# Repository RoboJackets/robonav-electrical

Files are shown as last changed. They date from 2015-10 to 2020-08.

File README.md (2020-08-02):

RoboNav Electrical
==========
Welcome to the electrcial repository of the RoboNav team! 

## Recommended Software (free)
- a [github account](https://github.com/join?source=header-home) 
    - the centralized location for all common files
- [git](https://git-scm.com/downloads)
    - popular version control system
    - quick [tutorial](https://try.github.io/levels/1/challenges/1)
- [EAGLE](https://www.autodesk.com/education/free-software/eagle)
    - CAD software for designing printed circuit boards (PCBs)

## Cloning the Repository
Now that you have all the required software, it's time to clone the repo!

To clone the repo, nagivate to the location in your computer where you would
like the repository using the change directory command in your terminal (cd):

```
cd desired-location
```

Now its time to clone:

```
git clone https://github.com/RoboJackets/robonav-electrical.git
```

You now have all you need to start contributing to the RoboNav Electrical team!

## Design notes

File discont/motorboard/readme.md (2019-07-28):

Motorboard has been renamed to logic board. The new files can be found on the upper level of directory

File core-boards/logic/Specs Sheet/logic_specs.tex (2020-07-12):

\documentclass[letterpaper, 12pt]{article}
\usepackage[letterpaper,margin=1in]{geometry}
\usepackage[english]{babel}
\usepackage{graphicx}
\usepackage{hyperref}
\usepackage{booktabs}
\usepackage[explicit]{titlesec}
\usepackage{fancyhdr}
\usepackage{inputenc}
\usepackage{enumitem,amssymb}
\usepackage{tikz}
\usetikzlibrary{arrows.meta}
\usetikzlibrary{calc}
\pagestyle{fancy}

\titleformat{\section}
  {\normalfont\Large\bfseries}{\thesection}{1em}{\hyperlink{sec-\thesection}{#1}
\addtocontents{toc}{\protect\hypertarget{sec-\thesection}{}}}
\titleformat{name=\section,numberless}
  {\normalfont\Large\bfseries}{}{0pt}{#1}
  
\titleformat{\subsection}
  {\normalfont\large\bfseries}{\thesubsection}{1em}{\hyperlink{subsec-\thesubsection}{#1}
\addtocontents{toc}{\protect\hypertarget{subsec-\thesubsection}{}}}
\titleformat{name=\subsection,numberless}
  {\normalfont\large\bfseries}{\thesubsection}{0pt}{#1}

\titleformat{\subsubsection}
  {\normalfont\large\bfseries}{\thesubsubsection}{1em}{\hyperlink{subsec-\thesubsubsection}{#1}
\addtocontents{toc}{\protect\hypertarget{subsec-\thesubsubsection}{}}}
\titleformat{name=\subsubsection,numberless}
  {\normalfont\large\bfseries}{\thesubsubsection}{0pt}{#1}

\newlist{todolist}{itemize}{2}
\setlist[todolist]{label=$\square$}
\usepackage{pifont}
\newcommand{\cmark}{\ding{51}}%
\newcommand{\xmark}{\ding{55}}%
\newcommand{\done}{\rlap{$\square$}{\raisebox{2pt}{\large\hspace{1pt}\cmark}}%
\hspace{-2.5pt}}
\newcommand{\wontfix}{\rlap{$\square$}{\large\hspace{1pt}\xmark}}

\begin{document}

\begin{titlepage}
\centering
	{\LARGE RoboJackets IGVC}\\
	\vspace{1cm}
	{\Large IGVC Logic Board 2019}\\
	\vfill
	{\large Created at November 18, 2017}\\
	\vspace{1cm}
	{\large Last Edited at \today\par}
\end{titlepage}

\tableofcontents

\pagebreak
% \section*{Todo Lists}
% \begin{todolist}
%   \item[\done] Update system diagram
%   \item[\done] Update relevant info
%   \item Schematics?
%   \item[\done] Sabertooth pinout
%   \item[\done] Indicator meaning
%   \item Lidar lites
%   \item Firmware
%   \item[\done] Estop system
% \end{todolist}

% \pagebreak

\section{Overview}
This document documents the functionality of the Logic Board (previously referred as \emph{motor board},
or Motor and Light Control Board in the year 2017 - 2018) in the IGVC subteam in \emph{RoboJackets}.
This document aims at providing the reader with the board's capability and limitation. \vspace{6pt}\\
The logic board is the interface between IGVC's software team and her actuators. Software team completes
path and motion planning in the onboard computer and sends driving commands via Ethernet to mbed on the Logic
Board, which then converts to Serial message to the Sabetooth motor controller.\\
\input{system_diagram.tex}

The primary function of the logic board contains the following:
\begin{itemize}
    \item Relay motor commands from software stack to motor controller and perform control algorithm in the process.
    \item Monitoring battery voltage and estop status, relay both to software stack.
    \item Communicate with the rest of electrical system and relay necessary information to the software stack.
\end{itemize}
Previous version of Logic board (motor and light) contains legacy interface for Open Source Motor Controller (OSMC)
which has been removed from the current version.

The motor board is controlled by an mbed NXP LPC1768 microcontroller development board (referred as mbed in the following). More details here: \url{https://os.mbed.com/platforms/mbed-LPC1768/} \vspace{6pt}\\
\pagebreak

\section{Hardware}
The motor board is designed using AutoDesk EagleCAD. Currently the PCB design files can be find under branch \texttt{rev/logic}
of \texttt{igvc-electrical} repository. Here's a link to master branch: \url{https://github.com/RoboJackets/igvc-electrical/}.

\subsection{Power System}
Four voltage level runs through this board. 
\begin{table}[h]
  % \boxed{
    \caption{Summary of functions of Voltage Levels}
    \centering
    \begin{tabular}{p{3cm}p{4cm}p{4cm}}
    \toprule
    Level ($V$)  & Direct Input Source & Maximum Ampere \\
    \midrule
    24V  & Robot Battery & ? \\
    12V  & 12V Rail & 3A  \\
    5V  & 12-5 Regulator & 1A \\
    3V3 & 5-3.3 Regulator & 300mA \\
    \bottomrule
    \end{tabular}
  % }
\end{table}

24V does not have a power plane on the motor board. The sole purpose of having 24V running
through this board is for battery voltage monitor. 24V will be divided between a 4.7k and
a 510 $\Omega$ resistor to achieve a voltage level of maximum 2.34V. The mbed reads in this value
from Analog pin \texttt{p19} to monitor the battery voltage. 

\begin{equation}
    V_{batt} = V_{in} \times 3.3 \times (4700 + 510) / 510 
\end{equation}

\vspace{1em}The rest of the power planes are shown on Figure \ref{fig:pwr_plane}.\\

12V plane is the main power source for the motor board. 12V plane powers the 5V plane via
12V-5V regulator (T1). LED under-glow, flood light and safety light resides on this power
plane. Each with components of sufficient ampere rating. \\

5V plane powers the mbed, encoder and the USB port to the PC. 5V plane powers the 3V3 plane
via the 5V-3V3 regulator, while the 3V3 plane only powers the imu and the ethernet port. \\

\begin{figure}[h]
\centering
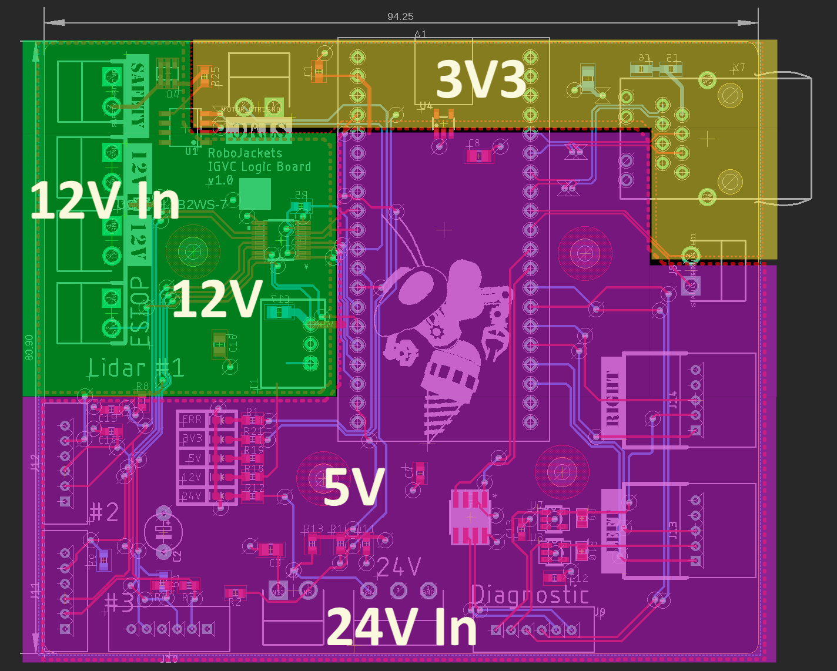
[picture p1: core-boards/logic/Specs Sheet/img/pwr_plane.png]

\caption{Power Plane Indication} \label{fig:pwr_plane}
\end{figure}

Each power plane has a dedicated LED indicator, indicating that this specific power plane
has been powered up. Notice that when \textbf{only} USB(either to mbed or X1 port) is connected,
without 12V power, 12V LED may still light up. This is caused by the internal design of 12-5 regulator.
The fact that 12V LED will light up only dimly suggest that 12V plane does not run 12V at this point.
It is \textbf{STRONGLY DISCOURAGED} to power the logic board solely by the mbed or USB port.

\begin{figure}[h]
  \centering
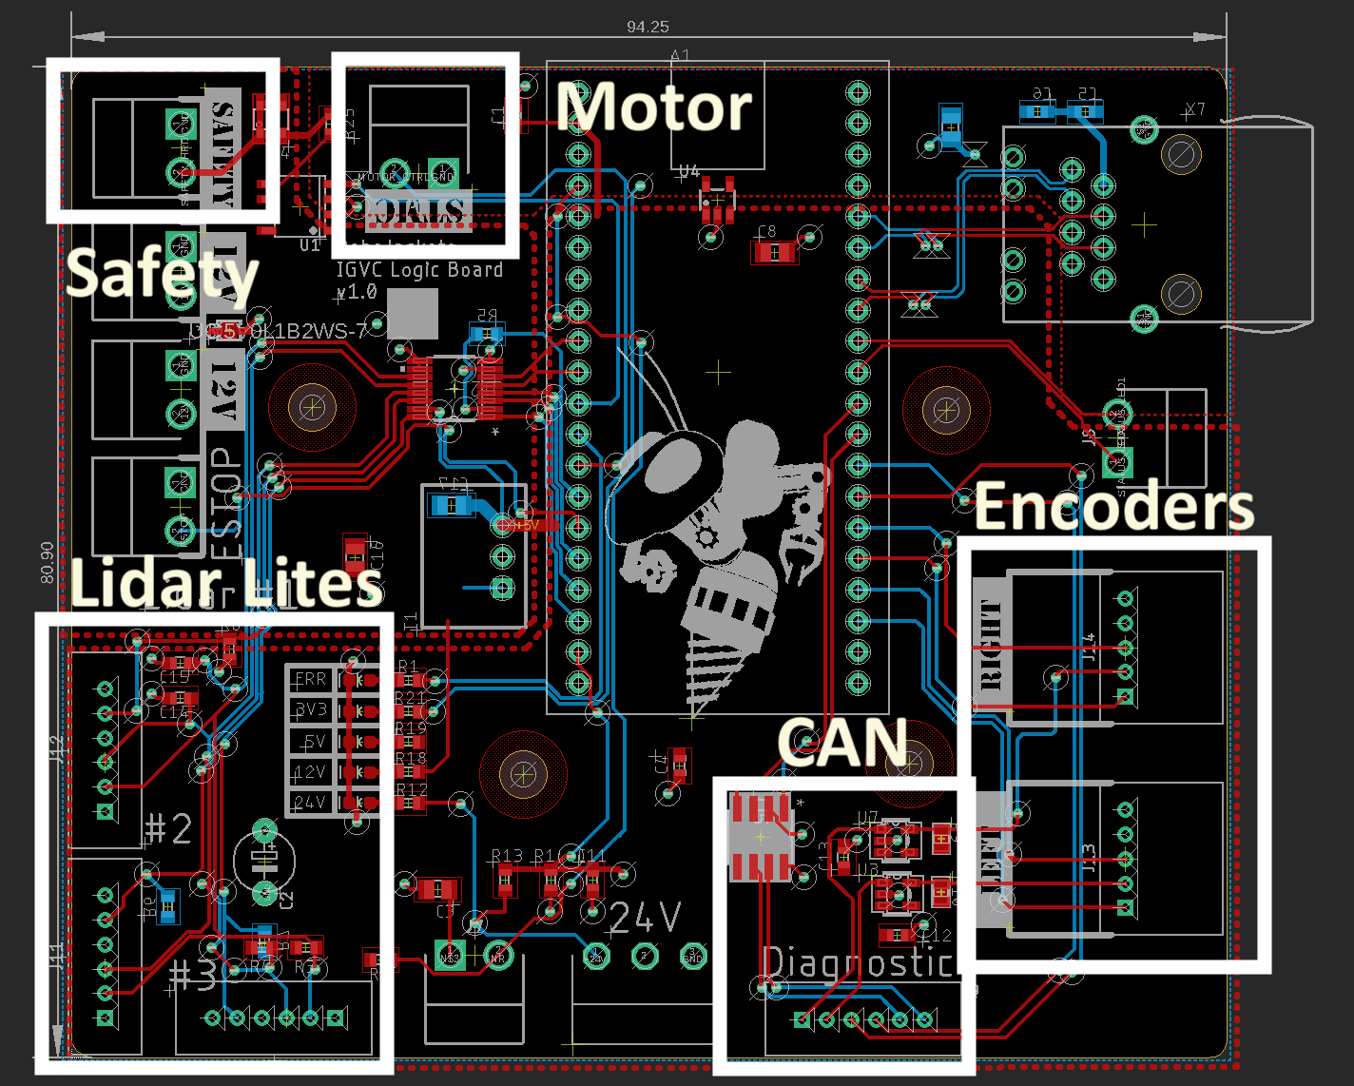
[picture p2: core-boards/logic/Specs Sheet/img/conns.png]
  
  \caption{Power Plane Indication} \label{fig:conns}
  \end{figure}

\subsection{Motor Control}

The connection port on the board can be found labeled in Figure \ref{fig:conns}.

Logic board interface with an off-the-shelf motor controller to control the IGVC motors. Logic board itself
does not run any high power current through the board. Motors on the IGVC robot is controlled by the
Sabertooth 2x60 A motor controller. Data sheets can be found here:
\url{https://www.dimensionengineering.com/products/sabertooth2x60}.\\

Motor board communicate with Sabertooth motor controller via a one-line serial communication
(the "Simplified Serial Communication" Mode). Only \textbf{tx} line on mbed is used, Sabertooth
does not send back any data and \textbf{rx} line on mbed may leave as not connected and used
for other purposes.\\

Port S1 is used for connection to sabertooth motor controller. The serial line connects to port
S1 on the sabertooth motor controller. For switch and other specific configurations, please refer
to the Sabertooth data sheet listed earlier. \\

The Logic board receives motor measurements through optical rotary encoders each with channel A and B.
Every change\footnote{or rise or fall, depending in firmware implementation} in tick would trigger an interrupt
function in the mbed code that increments the counter for angular displacement calculation. 

\subsection{Light Control}
Logic board controls the indicator light.\\

The indicator light is required by the competition rule that it should display different pattern
with regards to whether the robot is powered on or not and in autonomous mode or not. 
Logic board controls whether the light safety light is in flashy mode. The control signal comes from
the software stack.

Previously the motor and light Board contains a functionality for controlling underglows. This has been
moved offboard to a standalone board.

\subsection{Lidar Lites}

The lidar lites are for the concept of virtual bumper. Virtual bumper serves as an extra layer of sanity check to inform
the software stack that the robot is getting dangerously close to an obstacle. \\

The virtual bumper are formed via three Lidar Lites v3 water proof version that points outwards in forward, left and right 45 degrees fashion.
The are linked to the logic board via three six pin connectors and via I$^2$C protocol. Note that three lidar lites shares the same initial 
device address for I$^2$C therefore the design is to sequentially power them up and change the device address so that informations to every device
maybe retrieved. \\

Note that the overwritten device address would be \textbf{reset} after every power cycle. It is necessary to make the sequential power up part of the
regular routine of mbed code startup cycle. 

\subsection{Controller Area Network}

Controller Area Network, or CAN, are adapted on the board so that multiple boards may share the same message bus without the fear that the failure
of any board would bring down the entire network. 

Conventionally, for any micro-controller to join up in a CAN network, it would require that board to talk with a CAN controller, which then in turn
talk to the CAN transceiver that communicate on the CAN bus. The mbed has a built-in CAN controller and only a transceiver is present on the board. 
Be advised that the design of other board would require both a CAN controller and a CAN transceiver. 

\pagebreak

\section{Firmware}
Logic board firmware is currently undergoing an overhaul lead by Dallas Downing. You can find the code in 
\url{https://github.com/RoboJackets/igvc-firmware/tree/master/src/mbed}. mbed communicates with the computer via Ethernet
and Google's Protobuf library. 

\section{Control}
\subsection{PID Algorithm}
For software team to have a reliable localization, control over exact speed of motors are required.\\

Such control is done through PID algorithm in the motor board. PID stands for Proportional-Integral-Derivative controller. It operates on the idea that the output is changed based on the proportional, derivative and integral of difference between desired speed and actual speed over a certain $dT$. Details see \url{https://en.wikipedia.org/wiki/PID_controller}\\

Parameter values P, I and D need to be tuned for every different system. Increase proportional term value will increase the speed of the control system response, but will enlarge the overshoot and cause oscillation. Increase derivative term will cause the control system to react more strongly to changes in the error term, but will make the system unstable if the feedback signal is noisy. Increase integral term will sum overtime and drive the Steady-state error to zero, but will also increase the risk of a phenomenon called integral windup. \\

In short, PID need to be tuned, manually, especially if you're reading this document, since the robot probably has gone through a major remake and the system transfer function for the gear box + robot has changed.

\subsection{Emergency Stop}
In the event of IGVC robot goes terminator, absolute control over motor is required.\\

Emergency stop is the hardware stop for our robot that will physically cut power to motors,
done via a solenoid with diode magic circuits. The significance of Estop to the logic board
is that if the motors are cut power and motor board is still running PID algorithm, PID will
think power increase is not resulting in reduction of error, thus increase power output and
eventually reach maximum. When the robot is re-enabled, such error may cause robot to tip over. \\

A port is added to the motor board to accommodate this issue. Port marked "Estop" is for monitoring
estop status. In current electrical system design, when robot is stoped, this port will receive a +5V
signal and will be left floating when robot is enabled. This floating signal is complemented by mbed
pin's internal pull down configuration. 

This signal is further relayed to software stack in \texttt{robot enabled}. The logic board itself
does not perform any functionality in the estop system and does not need to be onboard the robot to test
the estop system.

\section{Miscellaneous}
\subsection{Expected Future Usage}
When the motor board was first designed, we left a ethernet port that was eventually utilized by IGVC for their
stability over simulated Serial port. So much that we have retired the USB port on the logic board. It is hard to
imagine what can be used for the future version of the logic board, since the control board now requires a major
revision as IGVC move towards swerve drive. There are always things to be done on the software level. It is not
hard to implement sensor fusion on the mbed and people should consider that possibility. After all, it is only
a small  embedded platform, robustness is of the most importance.

\subsection{Special Regards}
The author would like to thank Evan Peterson and Ryo Osawa from RoboJackets RoboCup team for their
awesome help in reviewing the design of board and much helpful advice. He would also like to thank
Jason Gibson from RoboJackets IGVC software team for his time in debugging Serial communication
problems with NUC.  

\subsection{Legacy Interfaces}
\textbf{NOT PRESENT IN LOGIC BOARD!}\\
IGVC robot Woodi (Year 2016 - 2017) and her predecessors used 4 Open Source Motor Controller (Referred as OSMC in the following) to control its motors. Current IGVC robot Jessi no longer uses OSMCs, yet a legacy port is reserved on the motor board in case for any unexpected incident. \vspace{6pt}\\
OSMCs are essentially H-bridge DC motor control circuits. Due to the specific design of OSMC, both switches on the high side of H-bridge are hard-wired to \textbf{CLOSED}. Therefore speed and direction control solely depends on the value of low side switches (see OSMC datasheet for specific control logic). The mbed has direct control over the low-side switches via PWMOut pins from p21 to p24. Be advised that one should \textbf{NEVER} set two low switches on the same H bridge to \textbf{CLOSED} at \textbf{ANY TIME}. \vspace{6pt}\\
The motor board used 2 Optoisolators chips to help control the low-side switches. Optoisolators keeps the motor board circuits electrically separated from the motor power circuits. Such design helps to protect the mbed from the fluctuation caused by motors. Although \emph{technically}, the mbed and the motor will still share the same ground level, having them not directly electrically connected through the motor board gives more time for the rest of the system to damp the fluctuation and protect the mbed. \vspace{6pt}\\
OSMC datasheets can be found here:\\
\url{http://www.robotpower.com/downloads/osmc3-22sch-clean.pdf}\\

\end{document}

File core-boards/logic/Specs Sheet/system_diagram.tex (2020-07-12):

% \begin{figure}[h]
%     \centering
%     \includegraphics[width=0.7\textwidth]{UpandLow.png}
%     \caption{motor board's Data Input and Output}
%     \end{figure}

\begin{figure*}[th]
    \centering
    \begin{tikzpicture}[inner sep=1em]
        \node[anchor=center, draw=black, rounded corners,] (pc) at (0in, 0in) {Computer};
        \node[anchor=center, draw=black, rounded corners,] (logic) at (0in, -1in) {Logic Board};
        \draw[{Latex[length=3mm]}-{Latex[length=3mm]}](pc.south)--(logic.north);
        \node[anchor=west] (ethernet) at (-0.5in, -0.5in) {Ethernet};

        \node[anchor=center, draw=black, rounded corners,] (sabertooth) at (-2in, -1in) {Sabertooth};
        \draw[{Latex[length=3mm]}-{Latex[length=3mm]}] (sabertooth.east)--(logic.west);
        \node[anchor=south] (serial) at (-1in, -1in) {Serial};
        \node[anchor=center, draw=black, rounded corners,] (motor) at (-2in, 0in) {Motor};
        \draw[{Latex[length=3mm]}-{Latex[length=3mm]}] (sabertooth.north)--(motor.south);
        \draw[{Latex[length=3mm]}-{Latex[length=3mm]}] (motor.south east) -- (logic.north west);
        \node[anchor=center, rotate=-27] at (-1in, -0.35in) {Encoder};
 
        \node[anchor=center, draw=black, rounded corners,] (safety) at (2in, 0in) {Safety Light};
        \draw[{Latex[length=3mm]}-] (safety.south west)--(logic.north east);

        \node[anchor=center, draw=black, rounded corners,] (estop) at (2in, -1in) {Estop Status};
        \draw[-{Latex[length=3mm]}] (estop.west)--(logic.east);

        \node[anchor=center, draw=black, rounded corners,] (diag) at (2in, -2in) {Diagnostic Board};
        \draw[{Latex[length=3mm]}-{Latex[length=3mm]}] (logic.south east)--(diag.north west);
        \node[anchor=center, rotate=-40] at (1in, -1.4in) {CAN};

        \node[anchor=center, draw=black, rounded corners,] (vrail) at (0in, -2in) {24V Rail};
        \draw[-{Latex[length=3mm]}] (vrail.north)--(logic.south);

        \node[anchor=center, draw=black, rounded corners,] (lidar) at (-2in, -2in) {Lidar Lites};
        \draw[{Latex[length=3mm]}-{Latex[length=3mm]}] (lidar.north east)--(logic.south west);
        \node[anchor=center, rotate=27] at (-1in, -1.35in) {I$^2$C};

    \end{tikzpicture}
    \caption{Logic board's Data Input and Output}
\end{figure*}

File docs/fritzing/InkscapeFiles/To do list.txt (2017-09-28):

1. Design/Draft info light to overall.fzz
2. Design light shield
3. Design motor shield
4. Design Safety light on

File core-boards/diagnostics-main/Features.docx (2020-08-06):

What do we want the main diagnostic board to do?

1. Main Board Components:
  a. Parts:
    i. ATMEGA2560 (MCU)
    ii. Two Pin Connector
      1. GND / VCC (5v)
    iii. Crystal (16 Mhz) (ECS-160-20-5PX-TR (https://www.digikey.com/product-detail/en/ecs-inc/ECS-160-20-5PX-TR/XC1282TR-ND/765265))
      1. Capacitors x2
    iv. Decoupling Capacitors
    v. Pull Up Resistor
2. Interface with the other mini boards:
  a. Specifically:
    i. Temperature Sensor
    ii. LED Feedback w/ Neopixels
    iii. Current Sensor
    iv. Decoupled Motor Detection
  b. How: Connectors using CAN bus communication or I^2C protocol
  c. What Parts:
    i. 5 Pin Connector (WM18933-ND) x 5
      1. GND / VCC (5v) / SDA / SCL
3. Interface with an external display
  a. How: Radio
  b. What Parts:
4. Interface with the Mast Status Panel:
  a. How: I2C
  b. What Parts:
5. Interface with Logic Board:
  a. How: 5 Pin Connector
  b. What Parts:
6. Interface with the Estop Board:
  a. How: 3 Pin Connector
  b. What Parts:
    i. Two Pin Connector
7. Read/Write to a SD Card
  a. How: SPI directly to the card
  b. What Parts:
    i. SD CARD
    ii. Level Shifter (5v -> 3v3)

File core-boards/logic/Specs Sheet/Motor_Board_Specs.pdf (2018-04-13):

# RoboJackets IGVC

## IGVC Motor and Light Control Board 2017

### Created at November 18, 2017

### Last Edited at April 13, 2018

CONTENTS | CONTENTS

## Contents

1 Overview | 2
2 Hardware | 4
3 Firmware | 7
4 Miscellaneous | 9
5 Special Regards | 10

1

1 OVERVIEW

## 1 Overview

This document explained the function of the Motor and Light Control Board (referred as motor board in the following) on RoboJackets IGVC subteam robot Jessi in the year 2017 - 2018 and showed how the board is designed with regards to its need, capability and limitation. This document is created in the hope that future RJ members can have a good understanding of the robot without unnecessary effort such as staring into the void and cursing whoever did the board without leaving a documentation.

The motor board is the interface between Jessi’s software control and her motor. IGVC software team completes path-planning on the onboard Intel NUC computing unit and will send driving command to the motor board. The motor board will tune the value according to PID and encoder value and then send it to the sabertooth motor controller, which will eventually power the motor.

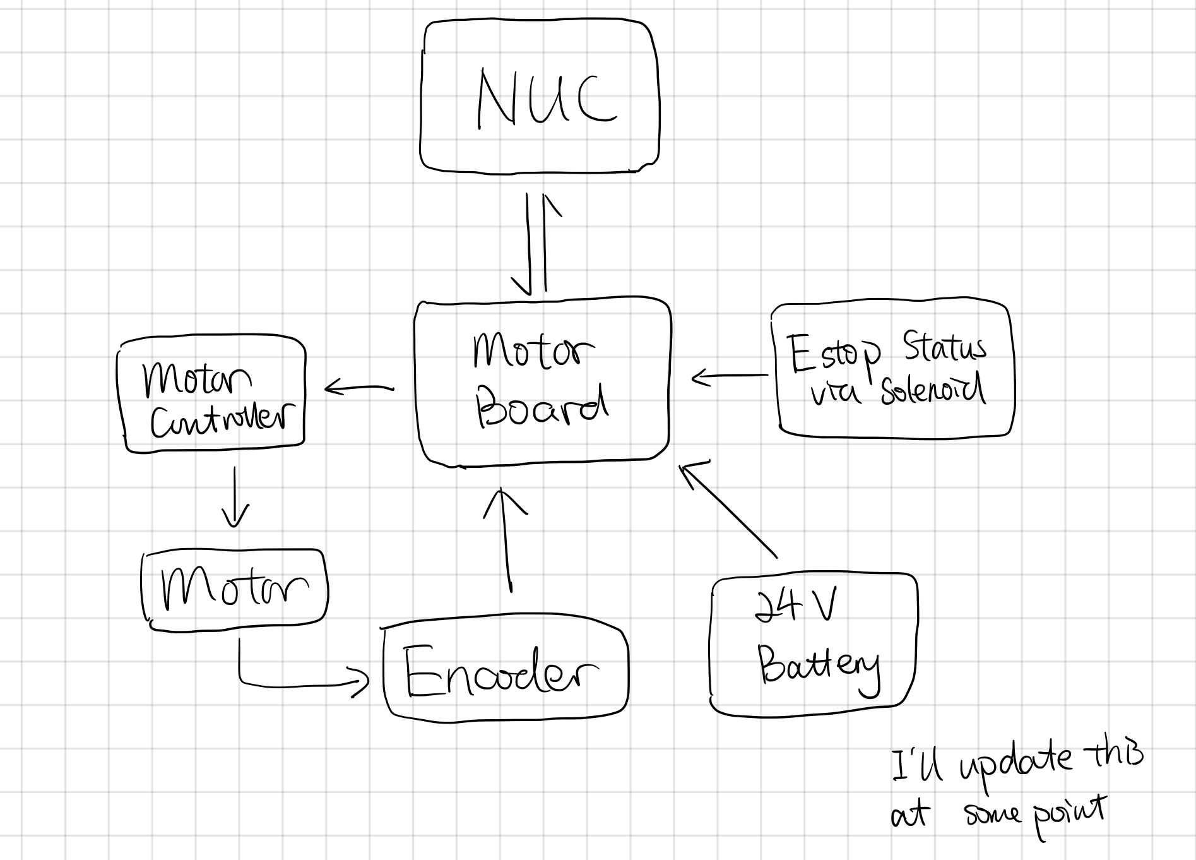
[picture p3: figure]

Figure 1: motor board’s Data Input and Output

The primary function of the motor board is to ensure the DC motors are operating at the speed desired by the NUC. Secondary functions include controlling the LED under-glow, monitoring battery voltage, E-stop status as well as Safety Light. The board also contained two ports for interfacing

2

1 OVERVIEW

with OSMCs, a legacy motor controller module RJ IGVC team used in the past. Each functioning circuits can operate independently from each other.

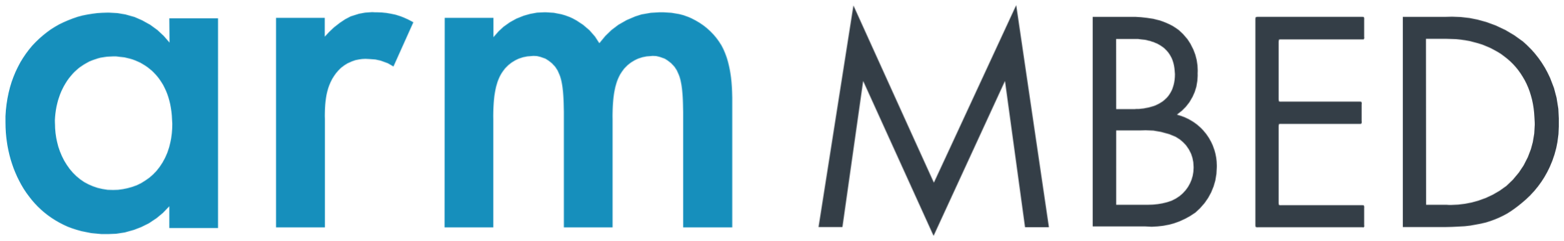
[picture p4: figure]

Figure 2: ARM logo

The motor board is controlled by an mbed NXP LPC1768 microcontroller development board (referred as mbed in the following). More details here: https://os.mbed.com/platforms/mbed-LPC1768/

3

2 HARDWARE

## 2 Hardware

The motor board is designed using AutoDesk EagleCAD. All PCB design files can be found under https://github.com/RoboJackets/igvc-electrical/tree/master/motorboard

### 2.1 Power System

Four voltage level runs through this board.

Table 1: Summary of functions of Voltage Levels
Level (V ) | Direct Input Source | Maximum Ampere
24V | Lithium Battery | ?
12V | 12V Rail | 3A
5V | 12-5 Regulator | 1A
3V3 | 5-3.3 Regulator | 300mA

24V does not have a power plane on the motor board. The sole purpose of having 24V running through this board is for battery voltage monitor. 24V will be divided between a 4.7k and a 510 ohm resistor to achieve a voltage level of maximum 2.34V. The mbed reads in this value from Analog pin p20 to monitor the battery voltage. Vbatt = Vin ∗ 3.3 × (4700 + 510)/510.

12V plane is the main power source for the motor board. 12V plane powers the 5V plane via 12V-5V regulator (T1). LED under-glow, flood light and safety light resides on this power plane. Each with components of sufficient ampere rating.

5V plane powers the mbed, encoder and the USB port to the NUC. 5V plane powers the 3V3 plane via the 5V-3V3 regulator, while the 3V3 plane only powers the imu and the ethernet port.

Each power plane has a dedicated LED indicator, indicating that this specific power plane has been powered up. Notice that when only USB(either to mbed or X1 port) is connected, without 12V power, 12V LED may still light up. This is caused by the internal design of 12-5 regulator. The fact

4

2.2 Motor Control | 2 HARDWARE

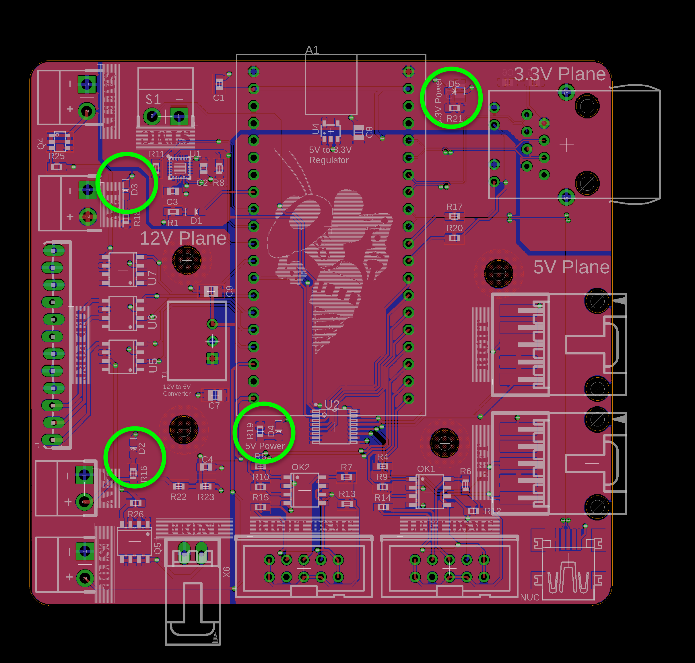
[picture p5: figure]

Figure 3: Power Indictor Circled Out

that 12V LED will light up only dimly suggest that 12V plane does not run 12V at this point. It is discouraged to power the motor board solely by the mbed or USB port.

### 2.2 Motor Control

Motor board interface with a separate motor controller to control the IGVC motors. Motor board itself does not run any high power current through the board. Motors on the IGVC robot is controlled by the Sabertooth 2x60 A motor controller. Data sheets can be found here: https://www.dimensionengineering.com/products/sabertooth2x60.

Motor board communicate with Sabertooth motor controller via a oneline serial communication (the ”Simplified Serial Communication” Mode).

5

2.3 Light Control | 2 HARDWARE

Only tx line on mbed is used, Sabertooth does not send back any data and rx line on mbed may leave as not connected and used for other purposes.

Port S1 is used for connection to sabertooth motor controller. The serial line connects to port S1 on the sabertooth motor controller. For switch and other specific configurations, please refer to the Sabertooth data sheet listed earlier.

### 2.3 Light Control

Motor board controls the indicator light and under-glow light bar.

The indicator light is required by the competition rule that it should display different pattern with regards to whether the robot is powered on or not and in autonomous mode or not. Motor board is capable of controlling such a light via port marked ”SAFETY”. The control signal, however, will come directly from NUC, since it can be implemented easier on NUC.

The under-glow light bar can be controlled directly via motor board. The under-glow is purely an aesthetic feature of the robot. Motor board have control over RGB values via PWMOut pins, (see schematics). The board has been designed to handle the current required.

6

3 FIRMWARE

## 3 Firmware

### 3.1 Interacting with NUC

Motor board communicates with NUC via Serial communication emulated by USBSerial interface. For more details, please see mbed OS 5 API. Serial communication via the onboard USB port

Motor board accepts a number of commands from NUC. At the startup of ROS, NUC would set parameters for PID algorithm and for most of the time, (20Hz and nonstop), NUC will be sending motor commands.The list of commands can be found in the following table, any character in parenthesis is optional. When the source is NUC, it’s always setting the value in motor board. When the source is motor board, it’s always returning a value to the NUC.

Motor board abbreviated as MB

Table 2: Summary of Serial Communication
Preamble | Format | Example | Source | Function
$ | $(-)X.X,(-)X.X | $-1.2,1.3 | NUC | Motor speed
#L | #LX | #L1 | NUC | Indicator light

#P | #PX.X,X.X | #P8.0,8.0 | NUC | PID P value

#D | #DX.X,X.X | #D8.0,8.0 | NUC | PID D value

$ | $(-)X.XX,
| (-)X.XX,0.XXX | $-1.25,1.13
| | ,0.051 | MB | Actual speed & dT
#V | #VXX.XX,X | #V24.23,1 | MB | Battery and Estop

When the communication is directly related to motor, the first value will always be for left motor and second for right. For example $1.2,-1.3 from NUC means the NUC want to set left motor be at 1.2m/s and right motor at reverse −1.3m/s.

7

3.2 Controlling the board | 3 FIRMWARE

### 3.2 Controlling the board

### 3.2.1 PID Algorithm

For software team to have a reliable localization, control over exact speed of motors are required.

Such control is done through PID algorithm in the motor board. PID stands for Proportional-Integral-Derivative controller. It operates on the idea that the output is changed based on the proportional, derivative and integral of difference between desired speed and actual speed over a certain dT. Details see https://en.wikipedia.org/wiki/PID_controller

Parameter values P, I and D need to be tuned for every different system. Increase proportional term value will increase the speed of the control system response, but will enlarge the overshoot and cause oscillation. Increase derivative term will cause the control system to react more strongly to changes in the error term, but will make the system unstable if the feedback signal is noisy. Increase integral term will sum overtime and drive the Steady-state error to zero, but will also increase the risk of a phenomenon called integral windup.

In short, PID need to be tuned, manually, especially if you’re reading this document, since the robot probably has gone through a major remake and the system transfer function for the gear box + robot has changed.

### 3.2.2 Emergency Stop

In the event of IGVC robot goes terminator, absolute control over motor is required.

Emergency stop is the hardware stop for our robot that will physically cut power to motors, done via a solenoid with diode magic circuits. The significance of Estop to the motor board is that if the motors are cut power and motor board is still running PID algorithm, PID will think power increase is not resulting in reduction of error, thus increase power output and eventually reach maximum. When the robot is re-enabled, such error may cause robot to tip over.

8

4 MISCELLANEOUS

A port is added to the motor board to accommodate this issue. Port marked ”Estop” is for monitoring estop status. In current electrical system design, when robot is stoped, this port will receive a +5V signal and will be left floating when robot is enabled. This floating signal is complemented by mbed pin’s internal pull down configuration.

## 4 Miscellaneous

### 4.1 Legacy Interfaces

IGVC robot Woodi (Year 2016 - 2017) and her predecessors used 4 Open Source Motor Controller (Referred as OSMC in the following) to control its motors. Current IGVC robot Jessi no longer uses OSMCs, yet a legacy port is reserved on the motor board in case for any unexpected incident.

OSMCs are essentially H-bridge DC motor control circuits. Due to the specific design of OSMC, both switches on the high side of H-bridge are hardwired to CLOSED. Therefore speed and direction control solely depends on the value of low side switches (see OSMC datasheet for specific control logic). The mbed has direct control over the low-side switches via PWMOut pins from p21 to p24. Be advised that one should NEVER set two low switches on the same H bridge to CLOSED at ANY TIME.

The motor board used 2 Optoisolators chips to help control the low-side switches. Optoisolators keeps the motor board circuits electrically separated from the motor power circuits. Such design helps to protect the mbed from the fluctuation caused by motors. Although technically, the mbed and the motor will still share the same ground level, having them not directly electrically connected through the motor board gives more time for the rest of the system to damp the fluctuation and protect the mbed.

OSMC datasheets can be found here: http://www.robotpower.com/downloads/osmc3-22sch-clean.pdf (http://www.robotpower.com/downloads/osmc3-22sch-clean.pdf)

9

4.2 Expected Future Usage | 5 SPECIAL REGARDS

### 4.2 Expected Future Usage

The motor board contains hardware feature not currently utilized. The Ethernet port (X7) is not currently used and the USB port (X1) is only used as Serial port, implemented as USBSerial in mbed firmware. The routing for traces connecting both port to the mbed have followed the layout rules for differential pair. If higher speed communication between the motor board and on-board computer is desired, these ports may be used.

## 5 Special Regards

The author would like to thank Evan Peterson and Ryo Osawa from Robo-Jackets RoboCup team for their awesome help in reviewing the design of board and much helpful advice. He would also like to thank Jason Gibson from RoboJackets IGVC software team for his time in debugging Serial communication problems with NUC.

10

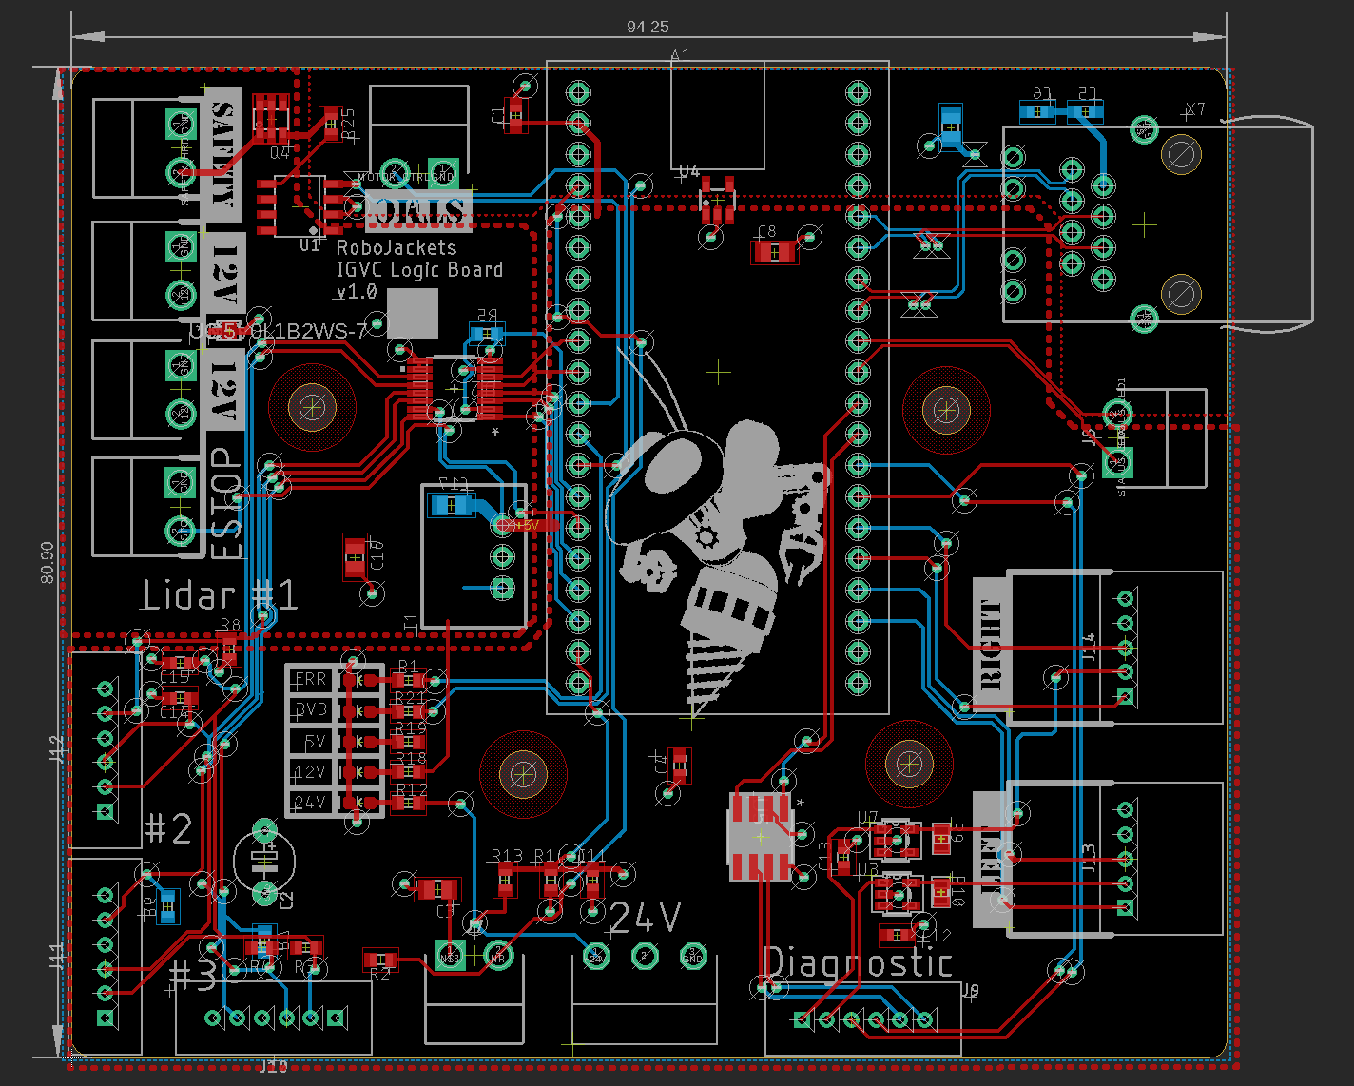
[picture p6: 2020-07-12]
core-boards/logic/Specs Sheet/img/default.png

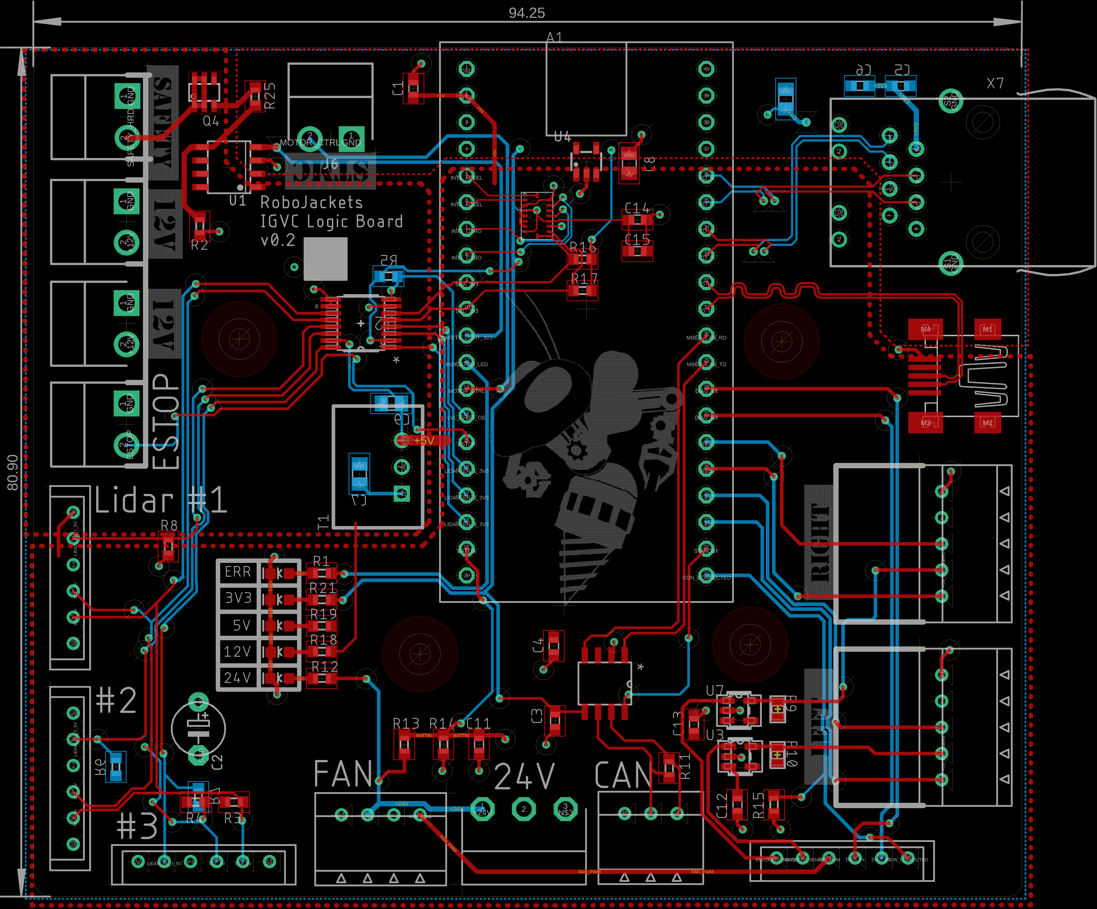
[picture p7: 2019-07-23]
core-boards/logic/Eagle Files/logic.png

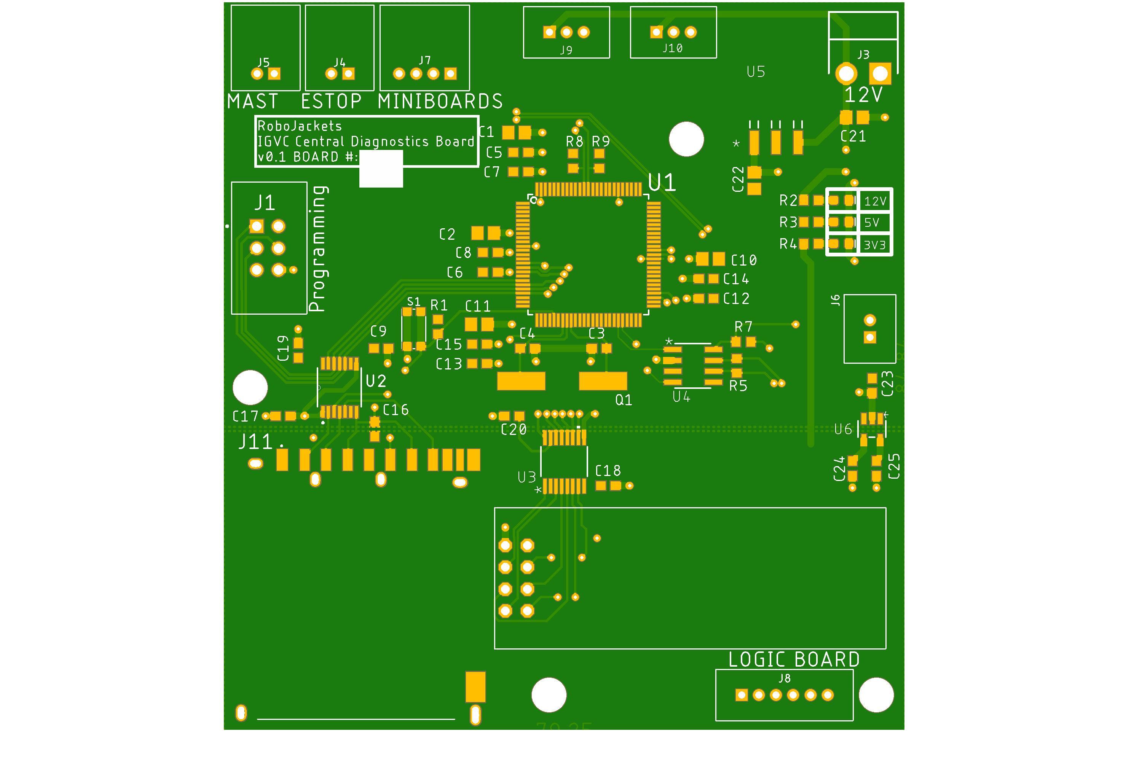
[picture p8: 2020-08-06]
core-boards/diagnostics-main/Eagle Files/diagnostic-main.png

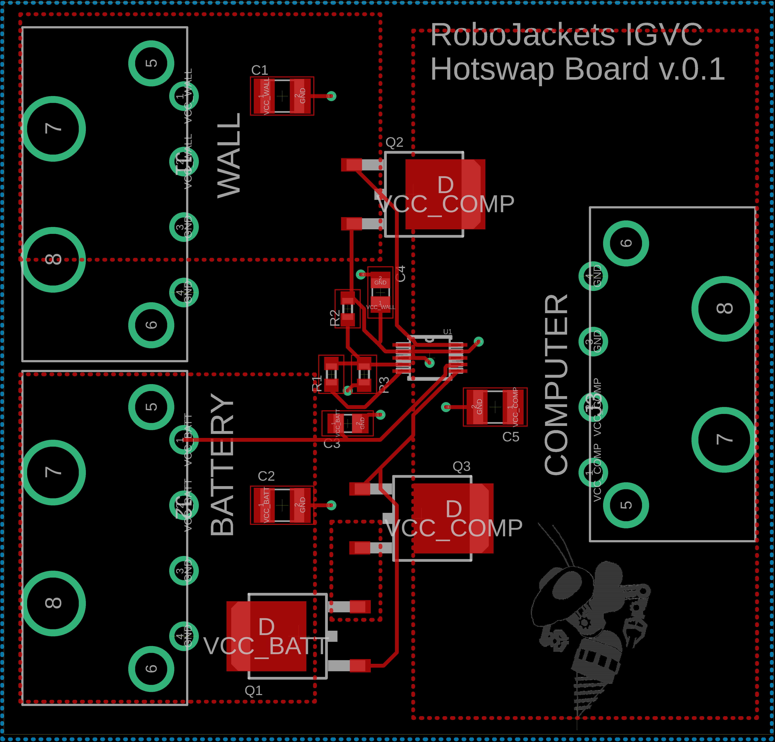
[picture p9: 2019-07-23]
core-boards/hotswap/hotswap.png

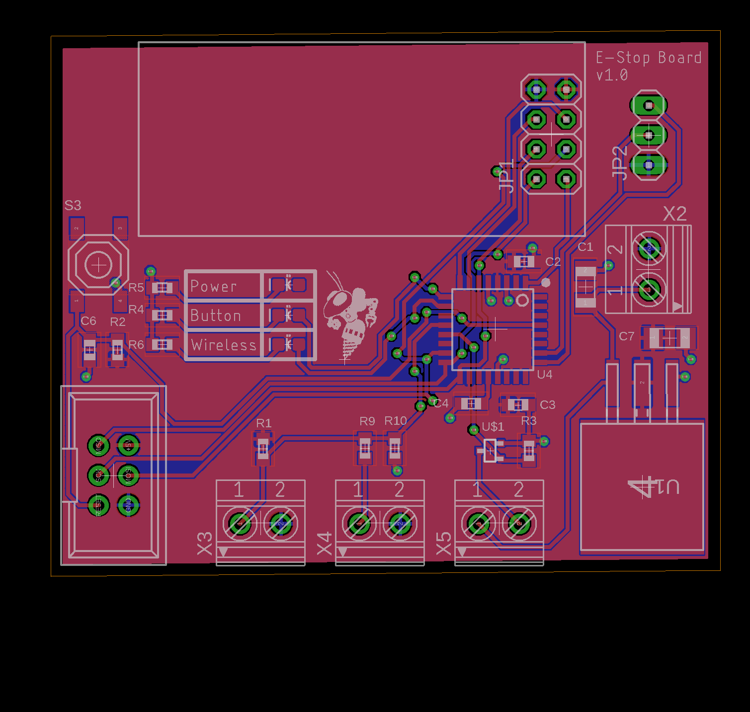
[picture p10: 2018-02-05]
core-boards/estop/Eagle Files/E-Stop Board v1.0.png

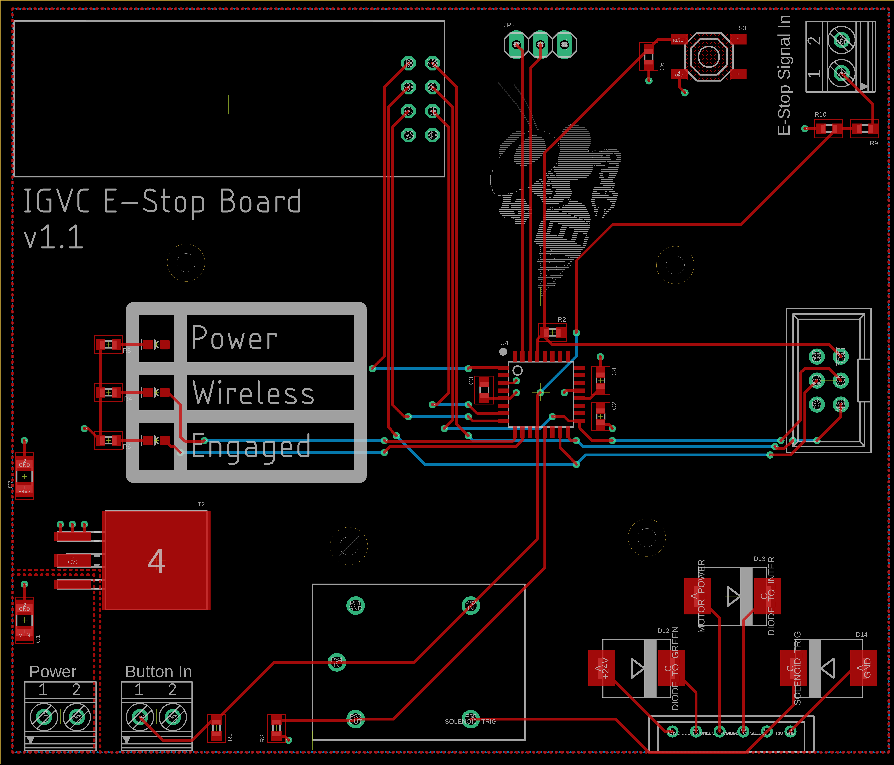
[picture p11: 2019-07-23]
core-boards/estop/Eagle Files/estop.png

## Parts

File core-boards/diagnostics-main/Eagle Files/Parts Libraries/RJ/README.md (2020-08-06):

# RoboJackets Eagle CAD Libraries

This repository contains unified libraries across the RoboJackets teams. New PCB repos should add this as a submodule.

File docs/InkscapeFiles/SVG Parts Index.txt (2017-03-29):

***This file contains all parts from the current IGVC Robot***
12V Lithium-acid Battery
Switch
24V Rail
GPS power Plug
PC battery Controller
E-stop Solenoid
Reciever
Arduino
Shunt
Battery Controller
Current Measure
Motor Shields
Encoder
24V to 12V Converter
Signal Light
E-stop Light
5V Converter

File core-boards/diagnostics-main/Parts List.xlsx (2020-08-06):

Part | Part Number / ID | Package | Digikey Link | #
16 Mhz Crystal | ECS-160-20-5PX-TR |  | https://www.digikey.com/product-detail/en/ecs-inc/ECS-160-20-5PX-TR/XC1282TR-ND/765265 | 1
Capacitor(10uF) | 1276-2405-1-ND | C0805 |  | 6
Capacitor(2.2uF) | 1276-1085-1-ND | C0603 |  | 1
Capacitor(1uF) | 1276-1182-1-ND | C0603 |  | 5
Capacitor(.1uF) | 490-10390-1-ND | C0603 |  | 10
Capacitor(.01uF) | 311-1596-1-ND | C0603 |  | 1
Capacitor(22pF) | 490-17301-1-ND | C0603 |  | 2
Resistor(10k) | 311-10.0KLRCT-ND | R0402 |  | 1
Resistor(2.2k) | 311-2.20KLRCT-ND | R0402 |  | 1
Resistor(1k) | 311-1.00KLRCT-ND | R0402 |  | 2
Resistor(120) | 311-120NCT-ND | R0402 |  | 2
Diode (Green) | P13485CT-ND | LED-0603 | https://www.digikey.com/product-detail/en/panasonic-electronic-components/LNJ326W83RA/P13485CT-ND/970685 | 3
Switch | 401-1426-2-ND | KMR2 | https://www.digikey.com/product-detail/en/c-k/KMR211GLFS/401-1426-2-ND/550475 | 1
Can Bus | 497-3930-1-ND |  | https://www.digikey.com/product-detail/en/microchip-technology/MCP2551T-I-SN/MCP2551T-I-SNCT-ND/9698145 | 1
Can Controller | MCP2515T-I/STCT-ND |  | https://www.digikey.com/product-detail/en/microchip-technology/MCP2515T-I-ST/MCP2515T-I-STCT-ND/4307903 | 1
SD Card Reader | A118090TR-ND |  | https://www.digikey.com/product-detail/en/te-connectivity-amp-connectors/1939870-1/A118090TR-ND/4731772 | 1
Radio | CC1101 |  | https://www.amazon.com/Solu-Wireless-Transceiver-Antenna-Arduino/dp/B00XDL9E64 | 1
Level Shifter (3v3 <-> 5v w/ 4 channels) | 296-38653-1-ND |  | https://www.digikey.com/product-detail/en/texas-instruments/LSF0204PWR/296-38653-1-ND/5056916 | 1
Level Shifter (3v3 <-> 5v w/ 6 channels) | 296-23759-1-ND |  | https://www.digikey.com/product-detail/en/texas-instruments/TXB0106PWR/296-23759-1-ND/1951146 | 1
Voltage Regulator (12v - 5v) | MCP2551T-I/SNCT-ND |  | https://www.digikey.com/product-detail/en/texas-instruments/LM1085ISX-5.0-NOPB/296-35391-1-ND/3739095 | 1
Voltage Regulator (5v - 3v3) | LP2985IM5X-3.3/NOPBCT-ND |  | https://www.digikey.com/product-detail/en/texas-instruments/LP2985IM5X-3.3-NOPB/LP2985IM5X-3.3-NOPBCT-ND/3527394 | 1
2 Pin Connector (Power) | 455-1648-ND |  | https://www.digikey.com/products/en?keywords=455-1648-ND | 1
2x3 Pin Connector | 3M15451-ND | 0.100" (2.54mm) | https://www.digikey.com/product-detail/en/3m/30306-6002HB/3M15451-ND/1237391 | 1
2x4 Pin Connector |  |  |  | 1
6 Pin Connector |  |  |  | 1
5 Pin Connector | WM4803-ND |  | https://www.digikey.com/product-detail/en/molex/0705430004/WM4803-ND/114927 | 1
3 Pin Connector | WM4900-ND |  | https://www.digikey.com/product-detail/en/molex/0705530001/WM4900-ND/114951 | 2
2 Pin Connector | 900-0022232021-ND |  | https://www.digikey.com/product-detail/en/molex/0022232021/900-0022232021-ND/26667 | 1

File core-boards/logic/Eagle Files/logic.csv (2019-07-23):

Qty | Value | Device | Package | Parts | Description
2 |  | R-US_R0603 | R0603 | R16, R17 | RESISTOR, American symbol
8 | 0.1uF | C-USC0603 | C0603 | C1, C3, C4, C5, C6, C11, C12, C13 | CAPACITOR, American symbol
1 | 100 | R-US_R0603 | R0603 | R25 | RESISTOR, American symbol
2 | 100nF | C-USC0603 | C0603 | C14, C15 | CAPACITOR, American symbol
4 | 10k | R-US_R0603 | R0603 | R5, R6, R7, R8 | RESISTOR, American symbol
3 | 10uF | C-USC0805 | C0805 | C7, C8, C9 | CAPACITOR, American symbol
1 | 120 | R-US_R0603 | R0603 | R11 | RESISTOR, American symbol
1 | 1M | R-US_R0603 | R0603 | R2 | RESISTOR, American symbol
3 | 1k | R-US_R0603 | R0603 | R15, R19, R21 | RESISTOR, American symbol
1 | 1uF | C-USC0805 | C0805 | C10 | CAPACITOR, American symbol
1 | 2.2k | R-US_R0603 | R0603 | R18 | RESISTOR, American symbol
4 | 4.7k | R-US_R0603 | R0603 | R3, R4, R12, R13 | RESISTOR, American symbol
1 | 510 | R-US_R0603 | R0603 | R14 | RESISTOR, American symbol
1 | 680uF | CPOL-USE5-5 | E5-5 | C2 | POLARIZED CAPACITOR, American symbol
1 | 800 | R-US_R0603 | R0603 | R1 | RESISTOR, American symbol
5 | B2PS-VH(LF)(SN) | B2PS-VH(LF)(SN) | B2PS-CENTERED | J2, J3, J4, J5, J6 | Power Connector
4 | B6B-EH-A(LF)(SN) | B6B-EH-A(LF)(SN) | B6BEHALFSN | X4, X8, X9, X12
1 | BMI088 | BMI088 | BMI088 | U6
2 | ERJ-L06KF50MVRC0805N-L | ERJ-L06KF50MVRC0805N-L | RC0805N-L | R9, R10
2 | GREEN | LED-BLUE0603 | LED-0603 | D2, D3 | Blue SMD LED
2 | GREEN | LED-GREEN0603 | LED-0603 | D4, D5 | Green SMD LED
2 | INA198AIDBVR | INA198AIDBVR | DBV5 | U3, U7
1 | MBED1768 | SPARKFUN-BOARDS_MBED_NXP_LPC1768 | SPARKFUN-BOARDS_DIL40_0.9 | A1 | mbed LPC1768 board footprint
1 | MCP2562-I/SN | MCP2562-I/SN | SOIC8-N_MC | U5
1 | MINI-USB_SHIELD5P4-32005-400 | MINI-USB_SHIELD5P4-32005-400 | 32005-400 | X1 | MINI USB-B R/A W/O POST 5 pol.
1 | R-78E5.0-1.0 | R-78E5.0-1.0 | R-78E | T1
1 | RED | LED-BLUE0603 | LED-0603 | D1 | Blue SMD LED
1 | S3B-EH(LF)(SN) | S3B-EH(LF)(SN) | S3BEHLFSN | X11
1 | S3B-VH | S3B-VH | S3B-VH | J1
2 | S5B-EH | S5B-EH | S5BEHLFSN | X2, X3
1 | S6B-EH(LF)(SN) | S6B-EH(LF)(SN) | S4BEHLFSN | X10
1 | SI-50170 | SI-50170 | SI-50170 | X7 | Ethernet Connector MagJack (R)
1 | STT4P3LLH6 | STT4P3LLH6 | SOT23-6 | Q4
1 | TC4427ACOA713 | TC4427ACOA713 | SOIC-8 | U1
1 | TLV70233DBVR | TLV70233DBVR | SOT-23-5 | U4
1 | TXB0106PWRPW16-M | TXB0106PWRPW16-M | PW16-M | U2

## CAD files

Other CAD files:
core-boards/logic/Enclosure/enclosure.ipt

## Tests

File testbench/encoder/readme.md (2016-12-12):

# RoboJackets IGVC Encoder Test bench
This document will give a brief description of the Test bench.

# Rotary Encoder
The encoder used in our IGVC robot is an optical encoder that uses the count of interruptions and the time interval between each two interruptions to determine the angle and angular velocity the motor has turned.
The encoder uses two optical sensors so that the direction of rotation can be determined by comparing the order of interruption of the two sensors.

# Test Bench
The test bench uses MCU (Microcontrollers Unit) to process encoder input signal and display the angle turned and angular velocity on a LCD(Liquid Crystal Display).
The test bench energy input would be provided by a 9V battery. There are other ports on the test bench. One is an 3x2 6 pin spi, used for programming the MCU. The other two are connection ports for encoder.

## MCU
The MCU used in the testbench is an AVR ATMega, the same one used in Arduino Uno. Time oscillation is provided by an 16MHz crystal backed up by two 22pF capacitor.
The 5V input required by MCU would be provided after a voltage regulation of a 9V battery.

## LCD
The LCD used is an 16x2 LCD. Each row displaying one of the values (Angle turned and Angular velocity).

## Programming
The MCU would be programmed prior to installation. The test bench can also be programmed using an AVR pocket programmer, via the 6 pins on side of the test bench.

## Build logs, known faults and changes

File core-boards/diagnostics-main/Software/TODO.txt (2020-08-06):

1. Find out how to enable SPI for multiple different pins
2. Inputs for SD Card to write to the Log Files
3. Can Bus Code Completely

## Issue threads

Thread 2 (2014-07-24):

Power indicator on Motor Board V2

barulicm, 2014-07-24:
If/when we get the new motor board printed, let's add a light so it's easier to check the Arduino board's power status.

Closed 2019-06-11.

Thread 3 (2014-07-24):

Laptop Dropping Out

barulicm, 2014-07-24:
The laptop seemingly randomly drops out. Just loses all power, no shut down process. Not sure exactly why it's happening, but it has something to do with the laptop being plugged into our charger board.

Investigate, diagnose, and fix, if possible.

(May need to compare the 2013 board to the 2012 board to check for any differences.)

--Update Nov 10 2013--
Trimm and I did some tests to compare the old laptop board to the new laptop board. We noticed that the new board's output is a volt higher than the old board.

Currently, the new board has been taken off the robot and replaced with the old board for now.

we need to check component values and make sure the voltage difference isn't being caused by differences there.

--Update Nov 24 2013--
We discovered that the barrel connector to the laptop was not actually put together properly. We suspect that this might be related to the failures. We've repaired it and are waiting to test it.

--Update Jul 24 2014--
Migrated to GitHub because this is still an issue even with the new barrel connector.

Closed 2019-06-11.

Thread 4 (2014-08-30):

Switch Between OSMCs and Motors

barulicm, 2014-08-30:
We need to add a switch that will open the circuit between the OSMCs and the motors. This is needed so that we can push the robot without having to unplugging the motors. The motors need to be disconnected from the OSMCs while pushing so they don't backpower the OSMCs and seize up the drive train.

NOTE: this feature is not needed on Misti, because it will be handled with mechanical disconnects on the wheels.

Closed 2019-06-11.

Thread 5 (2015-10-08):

Documentation

barulicm, 2015-10-08:
- [ ] EStop (Ben & Jose)
- [ ] 24V Rail (Will)
- [x] 12V Rail (Noah)
- [ ] 5V Rail (Sai)
- [ ] Motor Shield (Daniel & Chidi)
- [ ] Battery Monitor (Matt)

Closed 2019-06-11.

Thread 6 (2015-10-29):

Determine Monitor Power Requirements

barulicm, 2015-10-29:
http://www.newegg.com/Product/Product.aspx?Item=N82E16824009610
- voltage needed
- amperage needed (and/or power draw)
- connector type

sparkssss, 2015-10-29:
[IGVC_Monitor_Specifications.pdf](https://github.com/RoboJackets/igvc-electrical/files/22958/IGVC_Monitor_Specifications.pdf)

Voltage                     - 100 - 240 VAC, 50/60Hz
Power Consumption - Power Consumption (Energystar Off) (typ.): 0.33W
                                   Power Consumption (Energystar Sleep) (typ.): 0.41W
                                   **Power Consumption (Energystar On) (typ.): 16.87W**
Connector Type       - ADP-40PH BB (DELTA)
                                   DA-40A19       (APD)

Closed 2019-06-11.

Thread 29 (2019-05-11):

Pid should only be run when not estopped

oswinso, 2019-05-11:
Right now, integral builds up when estopped, which is dangerous.

Cryptum169, 2019-05-11:
This should be an implemented feature, at least it works in the past.

[Master branch](https://github.com/RoboJackets/igvc-electrical/blob/e4a296d3cfc413e7ea9bab4115781c89c67a9f74/motorboard/mbed%20firmware/main.cpp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)
[ethernet_ale branch](https://github.com/RoboJackets/igvc-electrical/blob/0e58067be9b5e8d480505fe47357ac25cb17fb2a/motorboard/mbed-firmware/main.cpp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)

JasonGibson274, 2019-05-11:
His recent change broke it since it does not clear I properly.

Closed 2019-07-21.

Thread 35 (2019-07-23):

Remove current branches

Cryptum169, 2019-07-23:
Remove branch `logic`, `led` and `wireless` once we confirm the merge back into master does not inflict bugs.

Cryptum169, 2019-08-01:
Address this again mid-fall term.

Closed 2020-07-17.

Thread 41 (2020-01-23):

estop_tx board 3.3v pwr doesn't work

Cryptum169, 2020-01-23:
Used level shifter to obtain 3.3v, didn't provide an reference source of voltage for level shifter to shift to, don't have 3.3v for the moment.

Potential fix: install a 5v to 3v3 from logic on estop tx to shift to 3.3v

Cryptum169, 2020-08-08:
Closing since this has been fixed on board design.

Closed 2020-08-08.

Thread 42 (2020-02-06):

estop_rx board has 24v going into microcontroller

Cryptum169, 2020-02-06:
The upstream signal from the mast gets converted to 5V and transmitted to MCU, and is not passed downstream. Control signal for relay would connect robot ground to MCU and relay itself.
Not enough to drive the solenoid.

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

Cryptum169, 2020-02-06:
Img from Estop circuit to explain what happens.
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

Cryptum169, 2020-07-17:
This has already been fixed , closing.

Closed 2020-07-17.

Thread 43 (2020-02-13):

estop radios are permanently reset

etillison3350, 2020-02-13:
The RFM9x radio has an active-low reset pin. On both the TX and RX E-Stop boards, these pins are being pulled down, so that the radio is permanently being reset. The reset pin should be either connected to a pin on the ATmega (preferred), or pulled high (so that it resets on power-on, only).

Cryptum169, 2020-08-08:
Closing since fixed on board design.

Closed 2020-08-08.

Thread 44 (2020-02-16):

Auto-reenable of estop system when Disengage button pulled out too fast.

Cryptum169, 2020-02-16:
System re-enables itself as motor controller keeps high charge, capacitance and resistance that prevents estop logic voltage from dropping.

Adding a relay between [Solenoid] <-> [Motor 24V] <-> [Relay] junction fixes this. This is verified through manual disconnection.

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

Cryptum169, 2020-02-22:
This has been implemented through the extra relay on the robot and verified/

Closed 2020-02-22.

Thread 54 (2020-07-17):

Tracking eagle libraries merge conflicts

Cryptum169, 2020-07-17:
Made the following two tables to help organize the conflicts of incoming merges.

|Branch| Edited Library|
|--|--|
| Hotswap| Connector; Discrete |
| Mast Panel | None |
|Remote Display | 296-21527-.lbr; Connector; Regulator; Switches |
| Neo-Pixel | Micro-controller |
| Fan ctrl | Micro controller, MCP9701 |
| estop-fix | Connector; Discrete; IC; Micro-controller; Regulator; Sensor|

- Connector
- [x] Hotswap
- [x] Remote Display
- Discrete
- [x] Hotswap
- [x] Estop-fix
- Regulator
- [x] Remote Display
- [x] estop-fix
- Switches
- [x] Remote Display
- Microcontroller
- [x] Neo pixel
- [x] Fan ctrl
- [x] Estop-fix
- IC
- [x] Estop-fix - Level Shifter TXB0104
- Sensor
- [x] Estop-fix - Only changes are layer addition, lbr directly overridden

Additionally, 296-21527 from Remote display branch and MCP9701 from fanctrl branch need to be merged into its respective type of libraries.

Cryptum169, 2020-07-17:
OOOOOK I went through the PRs and the good strategy here might be to add all the library changes in the branches to the master branch and use `git reset -- filename` to individually revert the .lbr files in the incoming branches.

This will requires us to keep two copies of the .lbr file and this can be done by
1. Open the master .lbr file
2. Library -> Manage Devices -> Import ... This will bring you to a `Add Parts` like window and it should be pretty straight forward from here on.

[This link](https://forums.autodesk.com/t5/eagle-forum/move-symbol-package-device-from-one-library-into-another/td-p/7168000) also claimed that you can drag and drop library devices, but I couldn't open two eagle instances on my mac so didn't test it, but if you can, _maybe_ that's an easier option.

I think it is safe to merge #52 as is, and let's split up the .lbr files works.

Cryptum169, 2020-07-17:
Just realized unprotected push to master was removed a few days ago ..., my changes to the library files will be on `fix/lbr_merge_1` branched from the latest `master`

Cryptum169, 2020-08-08:
Closing this since all incoming PR has been resolved.

Closed 2020-08-08.

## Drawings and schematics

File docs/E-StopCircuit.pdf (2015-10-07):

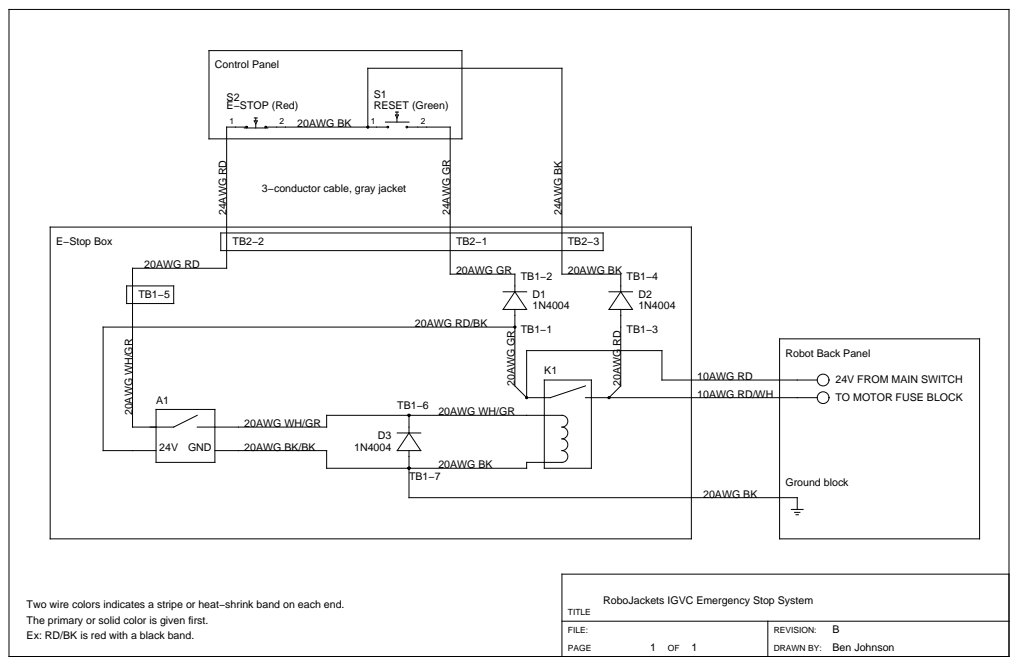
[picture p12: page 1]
PAGE; DRAWN BY:; 24V GND; 20AWG WH/GR; 20AWG BK; E−STOP (Red); RESET (Green); 10AWG RD/WH; 10AWG RD; 24V FROM MAIN SWITCH; Ground block; 20AWG BK/BK; 20AWG GR; 20AWG RDTB1−1 TB1−3; 20AWG RD/BK; 20AWG RD; 24AWG GR; 24AWG RD; 24AWG BK; Control Panel; E−Stop Box; Ben Johnson

3−conductor cable, gray jacket

20AWG GR | 20AWG BK

Robot Back Panel

TO MOTOR FUSE BLOCK

Two wire colors indicates a stripe or heat−shrink band on each end.
The primary or solid color is given first.
Ex: RD/BK is red with a black band.

RoboJackets IGVC Emergency Stop System

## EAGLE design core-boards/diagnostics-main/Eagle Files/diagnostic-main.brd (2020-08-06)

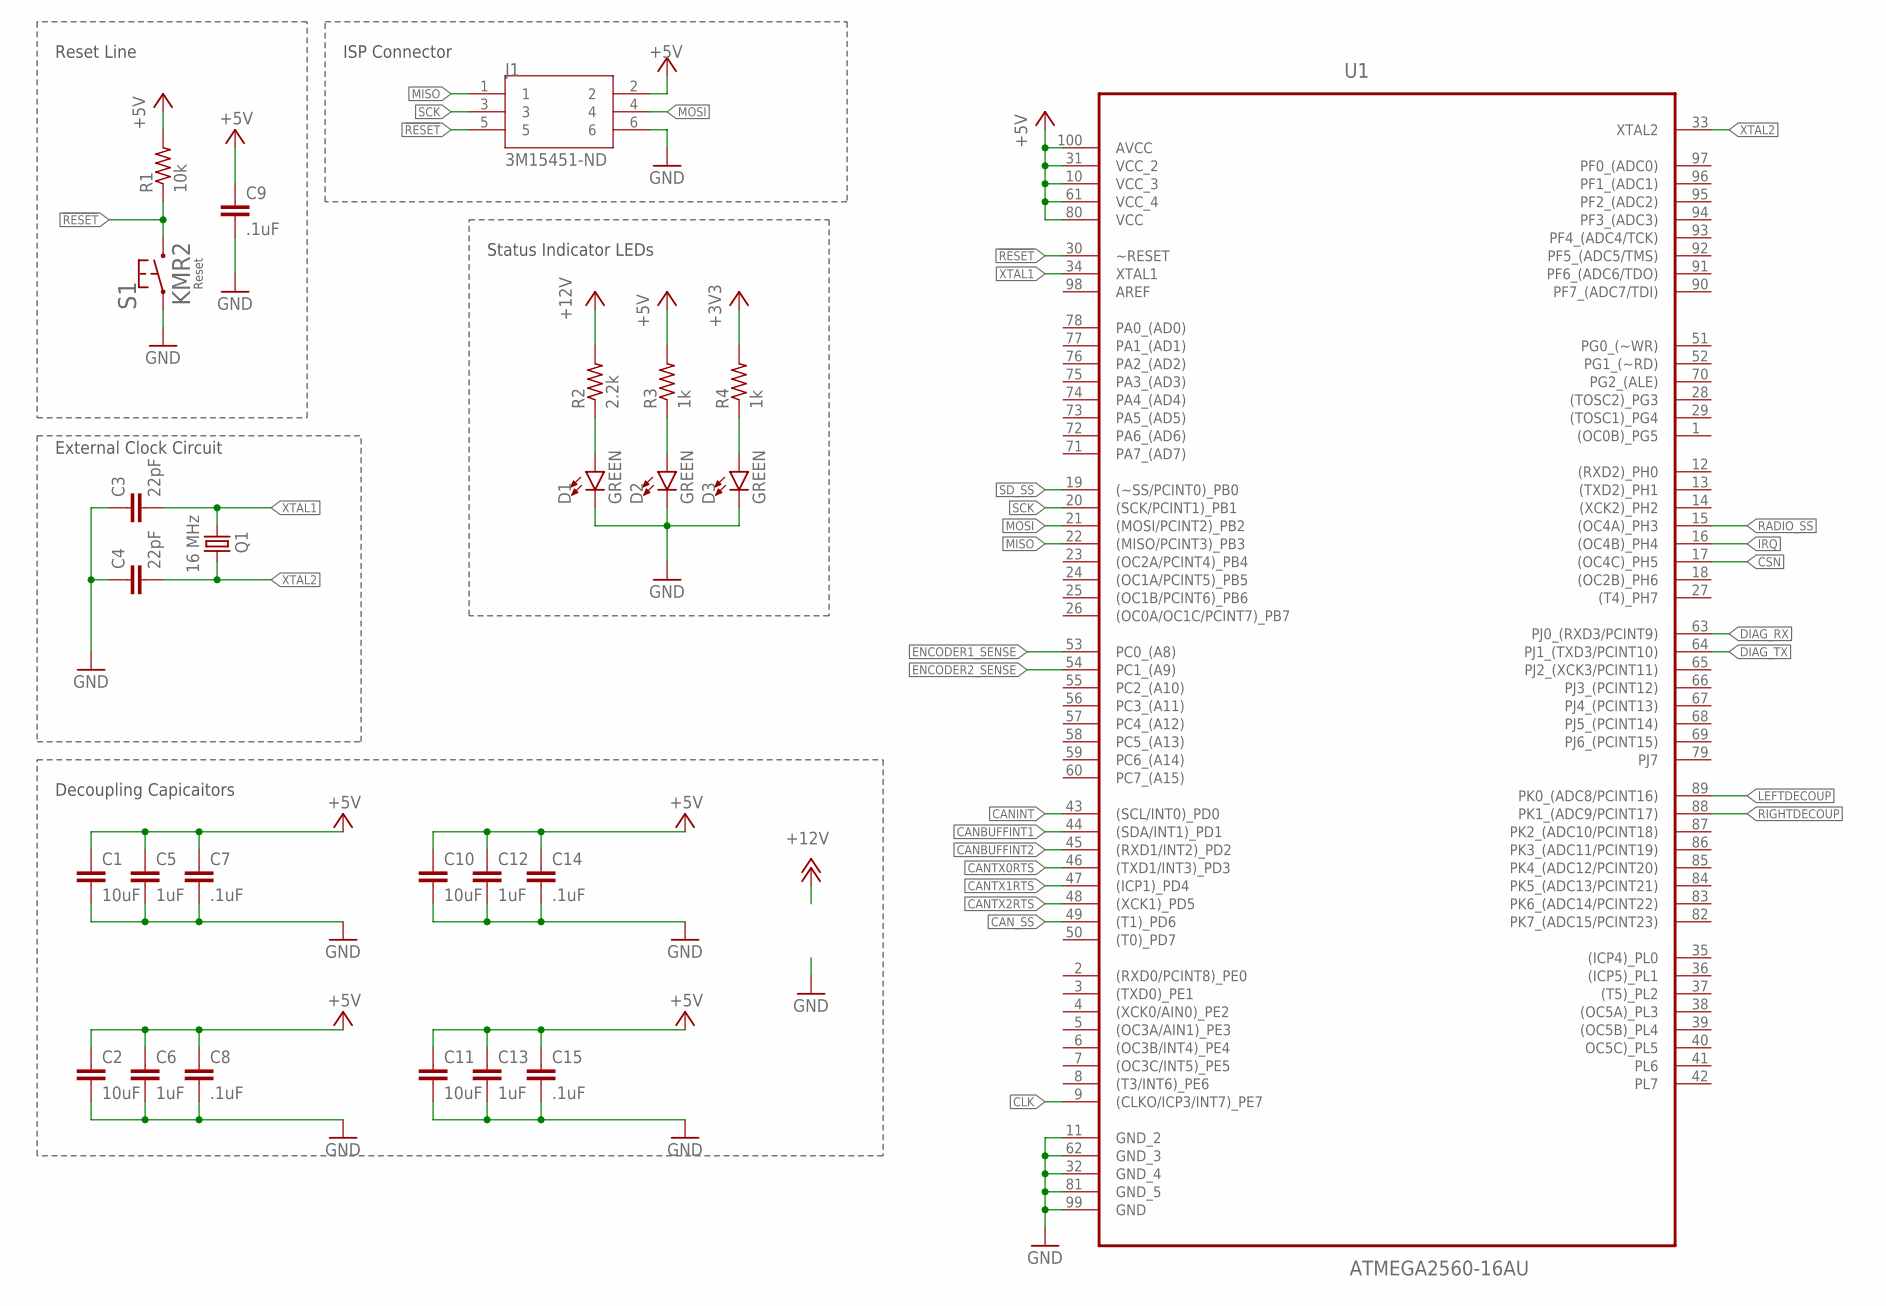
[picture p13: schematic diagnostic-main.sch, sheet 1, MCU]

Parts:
C1, C2, C10, C11: 10uF; C0805
C3, C4: 22pF; C0603
C5, C6, C12, C13: 1uF; C0603
C7, C8, C9, C14, C15: .1uF; C0603
D1, D2, D3: GREEN; LED-0603
J1: 3M15451-ND; 3M_30306-6002HB
Q1: 16 MHz; CSM-7X-DU
R1: 10k; R0603
R2: 2.2k; R0603
R3, R4: 1k; R0603
S1: KMR2
U1: ATMEGA2560-16AU; QFP50P1600X1600X120-100N

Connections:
3V3_LED_R: D3.A, R4.1
5V_LED_R: D2.A, R3.1
12V_LED_R: D1.A, R2.1
!RESET: J1.5, R1.1, S1.2.1 (2), S1.2.2 (2), U1.30 (~RESET)
+3V3: R4.2; also elsewhere on the board
+5V: C1.1, C2.1, C5.1, C6.1, C7.1, C8.1, C9.1, C10.1, C11.1, C12.1, C13.1, C14.1, C15.1, J1.2, R1.2, R3.2, U1.10 (VCC_3), U1.31 (VCC_2), U1.61 (VCC_4), U1.80 (VCC), U1.100 (AVCC); also elsewhere on the board
+12V: R2.2; also elsewhere on the board
CANBUFFINT1: U1.44 ((SDA/INT1)_PD1); also elsewhere on the board
CANBUFFINT2: U1.45 ((RXD1/INT2)_PD2); also elsewhere on the board
CANINT: U1.43 ((SCL/INT0)_PD0); also elsewhere on the board
CANTX0RTS: U1.46 ((TXD1/INT3)_PD3); also elsewhere on the board
CANTX1RTS: U1.47 ((ICP1)_PD4); also elsewhere on the board
CANTX2RTS: U1.48 ((XCK1)_PD5); also elsewhere on the board
CAN_SS: U1.49 ((T1)_PD6); also elsewhere on the board
CLK: U1.9 ((CLKO/ICP3/INT7)_PE7); also elsewhere on the board
CSN: U1.17 ((OC4C)_PH5); also elsewhere on the board
DIAG_RX: U1.63 (PJ0_(RXD3/PCINT9)); also elsewhere on the board
DIAG_TX: U1.64 (PJ1_(TXD3/PCINT10)); also elsewhere on the board
ENCODER1_SENSE: U1.53 (PC0_(A8)); also elsewhere on the board
ENCODER2_SENSE: U1.54 (PC1_(A9)); also elsewhere on the board
GND: C1.2, C2.2, C3.1, C4.1, C5.2, C6.2, C7.2, C8.2, C9.2, C10.2, C11.2, C12.2, C13.2, C14.2, C15.2, D1.C, D2.C, D3.C, J1.6, S1.1.1 (1), S1.1.2 (1), U1.11 (GND_2), U1.32 (GND_4), U1.62 (GND_3), U1.81 (GND_5), U1.99 (GND); also elsewhere on the board
IRQ: U1.16 ((OC4B)_PH4); also elsewhere on the board
LEFTDECOUP: U1.89 (PK0_(ADC8/PCINT16)); also elsewhere on the board
MISO: J1.1, U1.22 ((MISO/PCINT3)_PB3); also elsewhere on the board
MOSI: J1.4, U1.21 ((MOSI/PCINT2)_PB2); also elsewhere on the board
RADIO_SS: U1.15 ((OC4A)_PH3); also elsewhere on the board
RIGHTDECOUP: U1.88 (PK1_(ADC9/PCINT17)); also elsewhere on the board
SCK: J1.3, U1.20 ((SCK/PCINT1)_PB1); also elsewhere on the board
SD_SS: U1.19 ((~SS/PCINT0)_PB0); also elsewhere on the board
XTAL1: C3.2, Q1.1, U1.34 (XTAL1)
XTAL2: C4.2, Q1.2, U1.33 (XTAL2)

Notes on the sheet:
Reset Line
External Clock Circuit
Decoupling Capicaitors
ISP Connector
Status Indicator LEDs

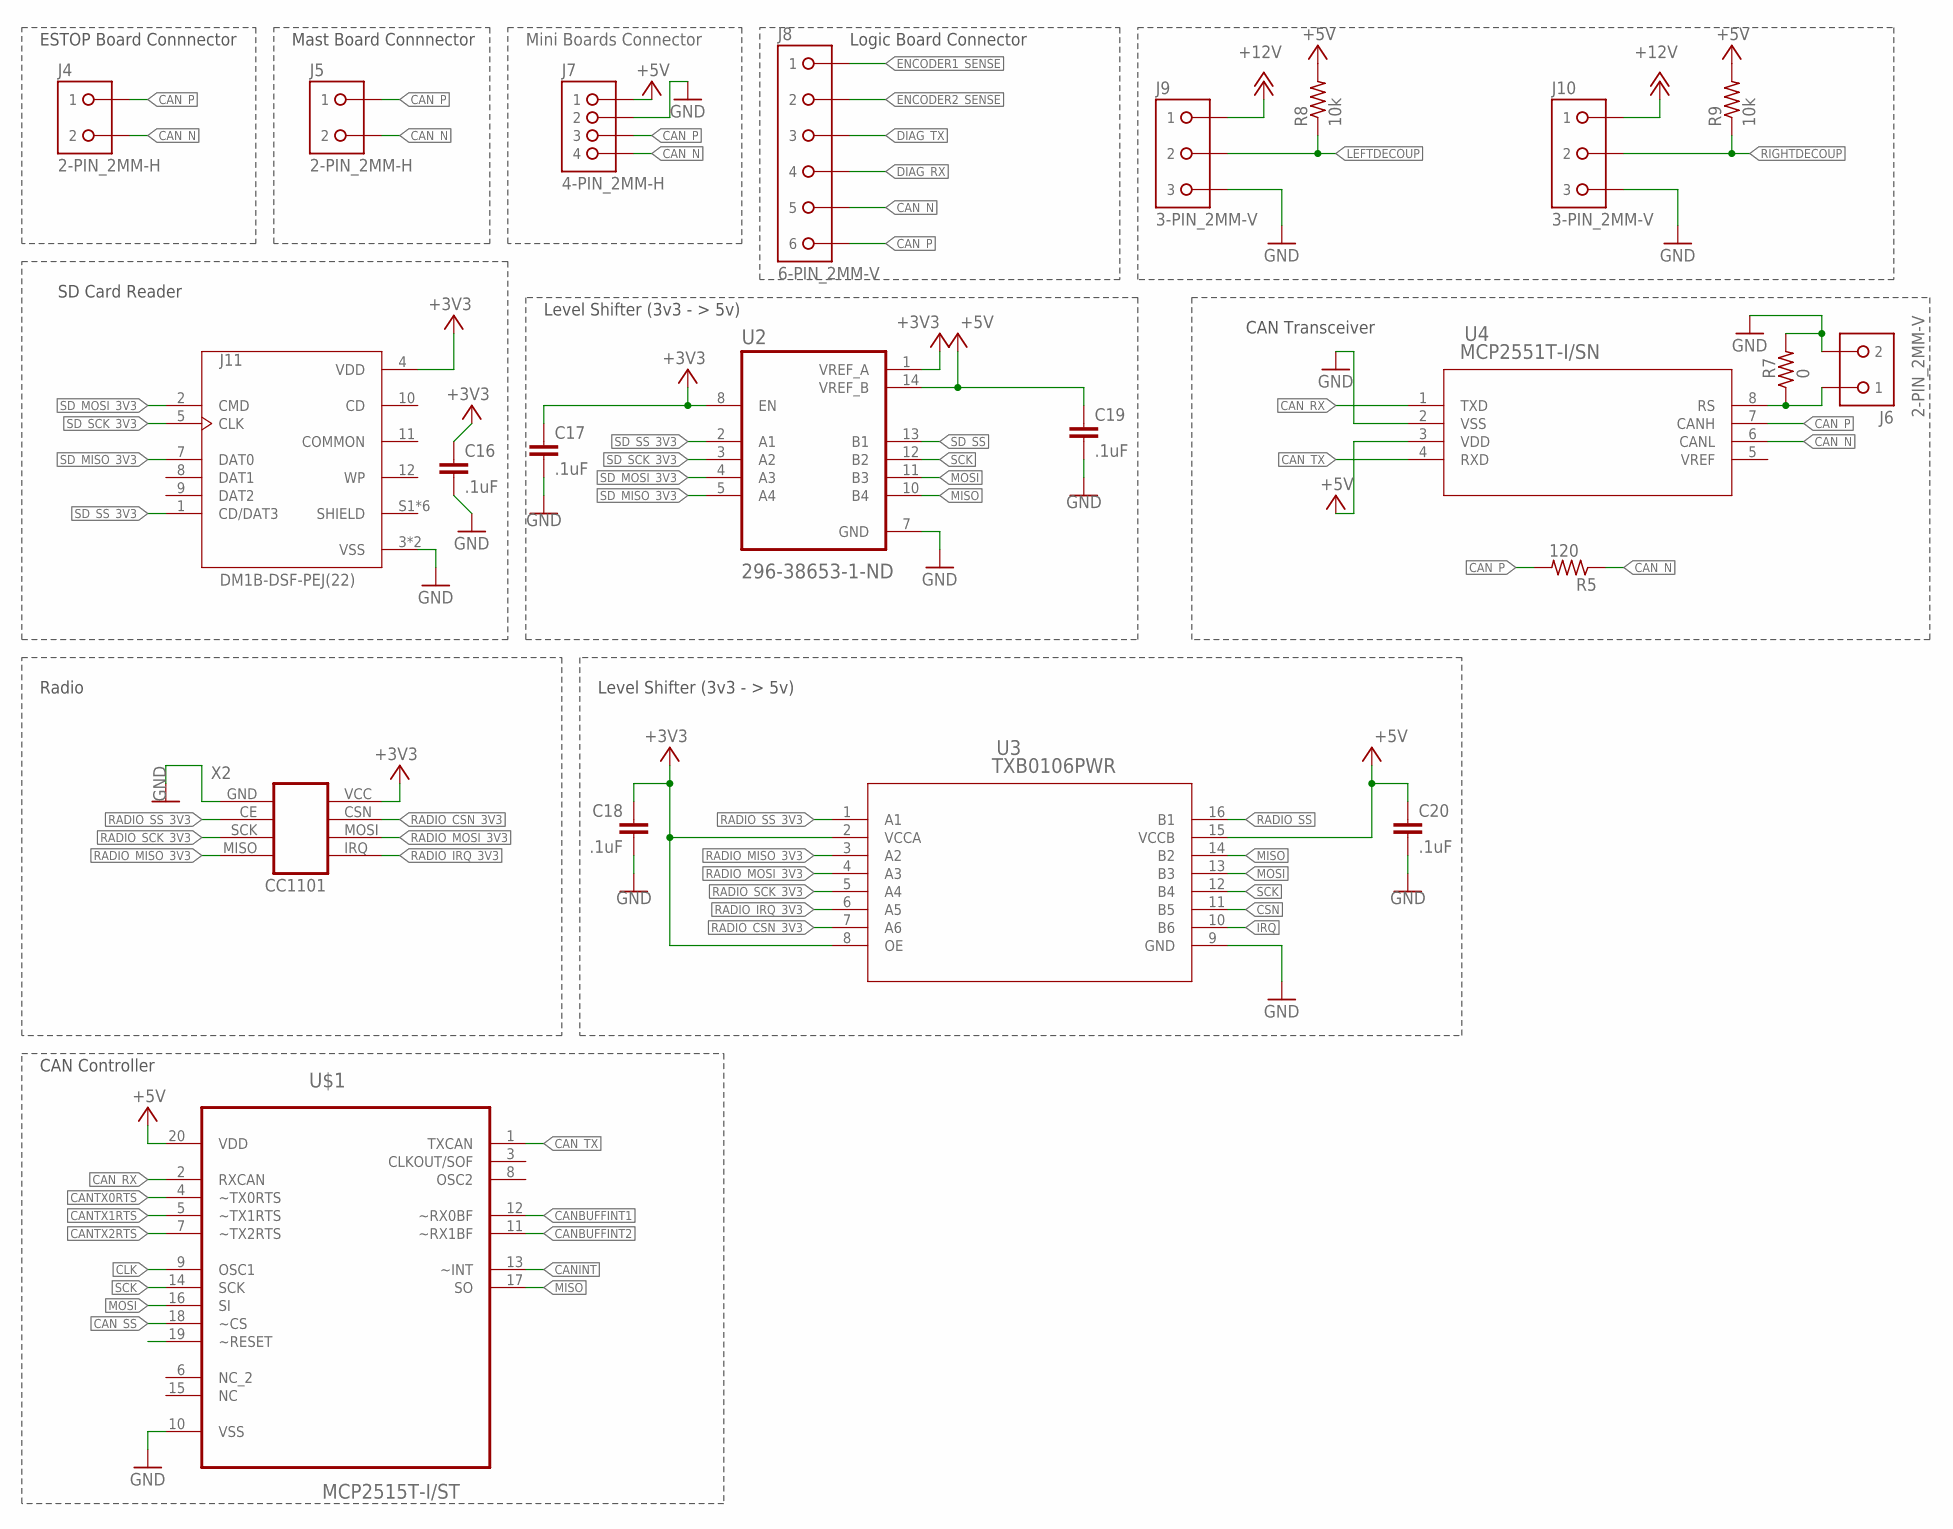
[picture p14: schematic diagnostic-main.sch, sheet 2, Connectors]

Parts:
C16, C17, C18, C19, C20: .1uF; C0603
J4, J5: 2-PIN_2MM-H; 2MM-2-H
J6: 2-PIN_2MM-V; 2MM-2-V
J7: 4-PIN_2MM-H; 2MM-4-H
J8: 6-PIN_2MM-V; 2MM-6-V
J9, J10: 3-PIN_2MM-V; 2MM-3-V
J11: DM1B-DSF-PEJ(22); JST_DM1B-DSF-PEJ(22)
R5: 120; R0603
R7: 0; R0603
R8, R9: 10k; R0603
U2: 296-38653-1-ND; SOP65P640X120-14N
U3: TXB0106PWR; PW16
U4: MCP2551T-I/SN; SOIC8-N_MC
U$1: MCP2515T-I/ST; SOP65P640X110-20N
X2: CC1101; NRF24L01+PA+LNA

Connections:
+3V3: C16.1, C17.1, C18.1, J11.4 (VDD), U2.1 (VREF_A), U2.8 (EN), U3.2 (VCCA), U3.8 (OE), X2.VCC; also elsewhere on the board
+5V: C19.1, C20.1, J7.1, R8.2, R9.2, U2.14 (VREF_B), U3.15 (VCCB), U4.3 (VDD), U$1.20 (VDD); also elsewhere on the board
+12V: J9.1, J10.1; also elsewhere on the board
CANBUFFINT1: U$1.12 (~RX0BF); also elsewhere on the board
CANBUFFINT2: U$1.11 (~RX1BF); also elsewhere on the board
CANINT: U$1.13 (~INT); also elsewhere on the board
CANTX0RTS: U$1.4 (~TX0RTS); also elsewhere on the board
CANTX1RTS: U$1.5 (~TX1RTS); also elsewhere on the board
CANTX2RTS: U$1.7 (~TX2RTS); also elsewhere on the board
CAN_N: J4.2, J5.2, J7.4, J8.5, R5.1, U4.6 (CANL)
CAN_P: J4.1, J5.1, J7.3, J8.6, R5.2, U4.7 (CANH)
CAN_RX: U4.1 (TXD), U$1.2 (RXCAN)
CAN_SS: U$1.18 (~CS); also elsewhere on the board
CAN_TX: U4.4 (RXD), U$1.1 (TXCAN)
CLK: U$1.9 (OSC1); also elsewhere on the board
CSN: U3.11 (B5); also elsewhere on the board
DIAG_RX: J8.4; also elsewhere on the board
DIAG_TX: J8.3; also elsewhere on the board
ENCODER1_SENSE: J8.1; also elsewhere on the board
ENCODER2_SENSE: J8.2; also elsewhere on the board
GND: C16.2, C17.2, C18.2, C19.2, C20.2, J6.2, J7.2, J9.3, J10.3, J11.3 (VSS), J11.6 (VSS), R7.2, U2.7 (GND), U3.9 (GND), U4.2 (VSS), U$1.10 (VSS), X2.GND; also elsewhere on the board
IRQ: U3.10 (B6); also elsewhere on the board
LEFTDECOUP: J9.2, R8.1; also elsewhere on the board
MISO: U2.10 (B4), U3.14 (B2), U$1.17 (SO); also elsewhere on the board
MOSI: U2.11 (B3), U3.13 (B3), U$1.16 (SI); also elsewhere on the board
RADIO_CSN_3V3: U3.7 (A6), X2.CSN
RADIO_IRQ_3V3: U3.6 (A5), X2.IRQ
RADIO_MISO_3V3: U3.3 (A2), X2.MISO
RADIO_MOSI_3V3: U3.4 (A3), X2.MOSI
RADIO_SCK_3V3: U3.5 (A4), X2.SCK
RADIO_SS: U3.16 (B1); also elsewhere on the board
RADIO_SS_3V3: U3.1 (A1), X2.CE
RIGHTDECOUP: J10.2, R9.1; also elsewhere on the board
RS: J6.1, R7.1, U4.8 (RS)
SCK: U2.12 (B2), U3.12 (B4), U$1.14 (SCK); also elsewhere on the board
SD_MISO_3V3: J11.7 (DAT0), U2.5 (A4)
SD_MOSI_3V3: J11.2 (CMD), U2.4 (A3)
SD_SCK_3V3: J11.5 (CLK), U2.3 (A2)
SD_SS: U2.13 (B1); also elsewhere on the board
SD_SS_3V3: J11.1 (CD/DAT3), U2.2 (A1)

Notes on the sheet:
ESTOP Board Connnector
SD Card Reader
Level Shifter (3v3 - > 5v)
Logic Board Connector
Mini Boards Connector
CAN Transceiver
Radio
Mast Board Connnector
CAN Controller

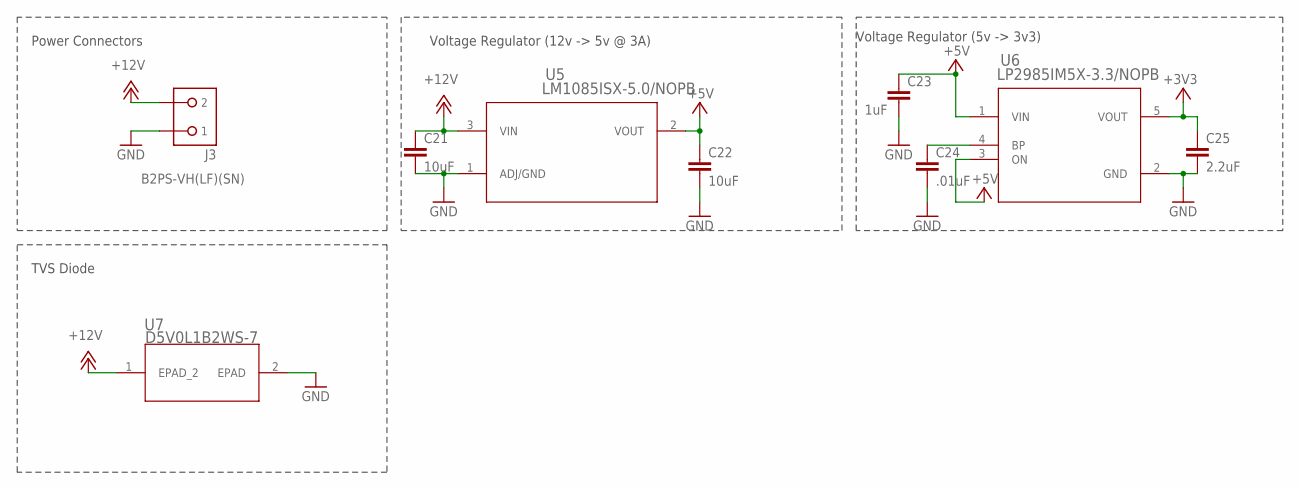
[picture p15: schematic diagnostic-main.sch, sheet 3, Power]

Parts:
C21, C22: 10uF; C0805
C23: 1uF; C0603
C24: .01uF; C0603
C25: 2.2uF; C0603
J3: B2PS-VH(LF)(SN); B2PS-CENTERED
U5: LM1085ISX-5.0/NOPB; TS3B
U6: LP2985IM5X-3.3/NOPB; MF05A
U7: D5V0L1B2WS-7; SOD323

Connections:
+3V3: C25.1, U6.5 (VOUT); also elsewhere on the board
+5V: C22.1, C23.1, U5.2 (VOUT), U6.1 (VIN), U6.3 (ON); also elsewhere on the board
+12V: C21.1, J3.2, U5.3 (VIN), U7.1 (EPAD_2); also elsewhere on the board
GND: C21.2, C22.2, C23.2, C24.2, C25.2, J3.1, U5.1 (ADJ/GND), U6.2 (GND), U7.2 (EPAD); also elsewhere on the board
unnamed: C24.1, U6.4 (BP)

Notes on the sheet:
Voltage Regulator (12v -> 5v @ 3A)
Voltage Regulator (5v -> 3v3)
Power Connectors
TVS Diode

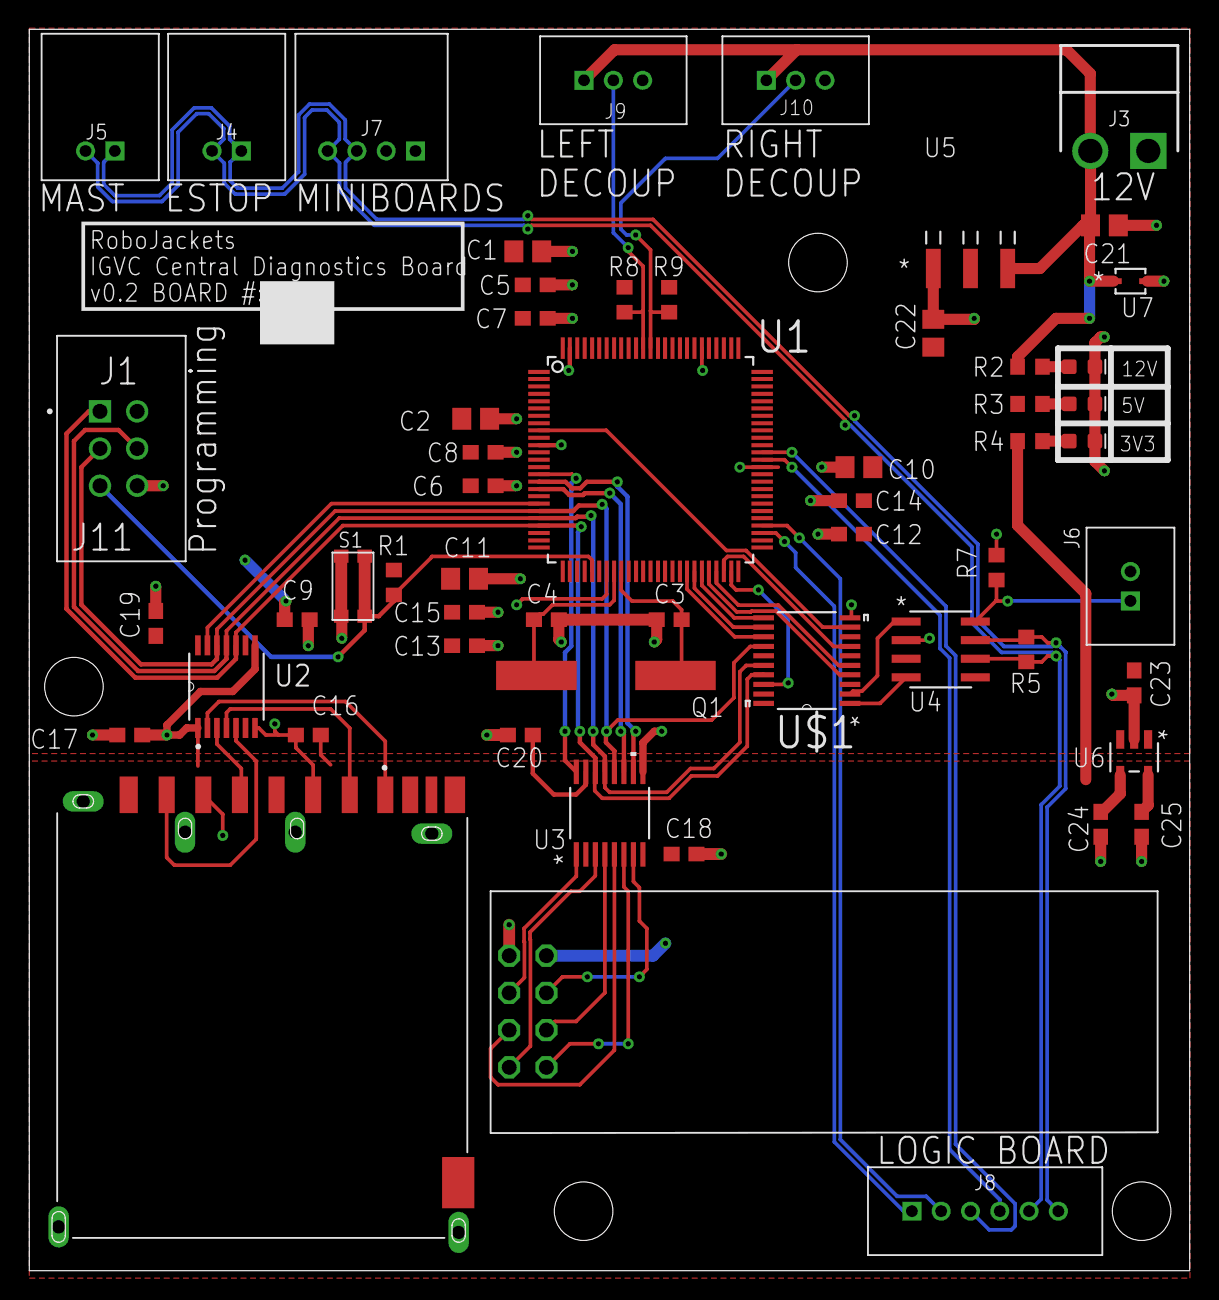
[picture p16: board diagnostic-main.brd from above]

Board: 2 copper layers, 79.2 x 84.8 mm, 57 parts (0 on the bottom side), 47 nets.

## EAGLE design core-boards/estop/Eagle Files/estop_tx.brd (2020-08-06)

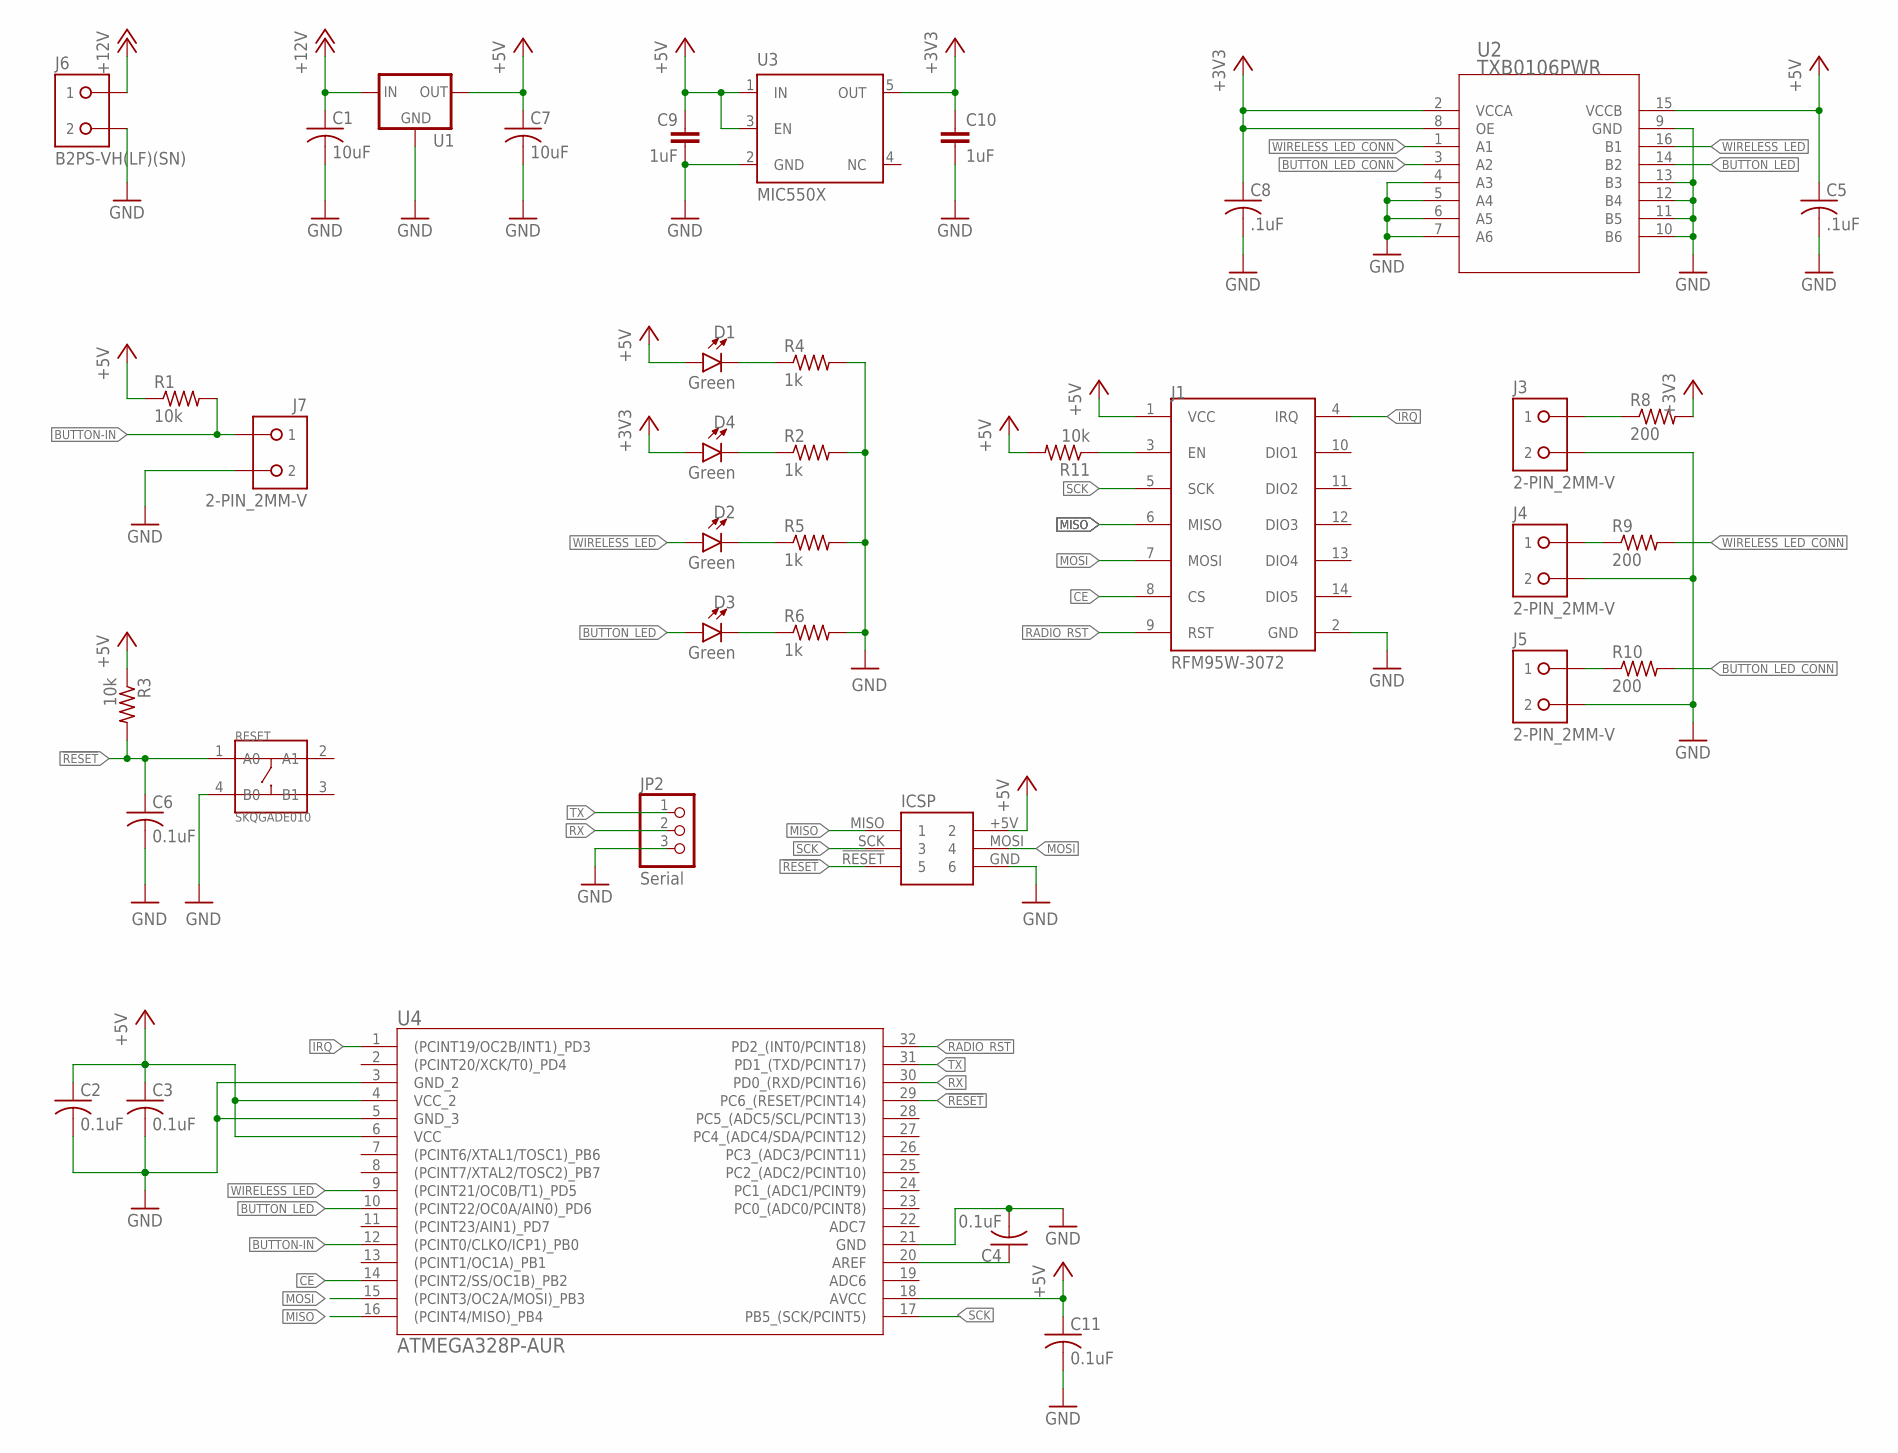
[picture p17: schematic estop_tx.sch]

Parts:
C1, C7: 10uF; C0805
C2, C3, C4, C6, C11: 0.1uF; C0603
C5, C8: .1uF; C0603
C9, C10: 1uF; C0603
D1, D2, D3, D4: Green; LED-0603
ICSP: ICSP Connector; 2X3SHROUDED
J1: RFM95W-3072
J3, J4, J5, J7: 2-PIN_2MM-V; 2MM-2-V
J6: B2PS-VH(LF)(SN); B2PS-CENTERED
JP2: Serial; 1X03
R1, R3, R11: 10k; R0603
R2, R4, R5, R6: 1k; R0603
R8, R9, R10: 200; R0603
RESET: SKQGADE010; SW4-SMD-5.2X5.2X1.5MM
U1: R-78E5.0-1.0CONV_R-78E5.0-1.0; CONV_R-78E5.0-1.0
U2: TXB0106PWR; PW16
U3: MIC550X; SOT23-DBV
U4: ATMEGA328P-AUR

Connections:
!RESET: C6.1, ICSP.!RESET (5), R3.2, RESET.1 (A0), U4.29 (PC6_(RESET/PCINT14))
+3V3: C8.1, C10.1, D4.A, R8.2, U2.2 (VCCA), U2.8 (OE), U3.5 (OUT)
+5V: C2.1, C3.1, C5.1, C7.1, C9.1, C11.1, D1.A, ICSP.+5V (2), J1.1 (VCC), R1.1, R3.1, R11.2, U1.3 (OUT), U2.15 (VCCB), U3.1 (IN), U3.3 (EN), U4.4 (VCC_2), U4.6 (VCC), U4.18 (AVCC)
+12V: C1.1, J6.1, U1.1 (IN)
BUTTON-IN: J7.1, R1.2, U4.12 ((PCINT0/CLKO/ICP1)_PB0)
BUTTON_LED: D3.A, U2.14 (B2), U4.10 ((PCINT22/OC0A/AIN0)_PD6)
BUTTON_LED_CONN: R10.2, U2.3 (A2)
CE: J1.8 (CS), U4.14 ((PCINT2/SS/OC1B)_PB2)
EN: J1.3 (EN), R11.1
GND: C1.2, C2.2, C3.2, C4.2, C5.2, C6.2, C7.2, C8.2, C9.2, C10.2, C11.2, ICSP.GND (6), J1.2 (GND), J3.2, J4.2, J5.2, J6.2, J7.2, JP2.3, R2.2, R4.2, R5.2, R6.2, RESET.4 (B0), U1.2 (GND), U2.4 (A3), U2.5 (A4), U2.6 (A5), U2.7 (A6), U2.9 (GND), U2.10 (B6), U2.11 (B5), U2.12 (B4), U2.13 (B3), U3.2 (GND), U4.3 (GND_2), U4.5 (GND_3), U4.21 (GND)
IRQ: J1.4 (IRQ), U4.1 ((PCINT19/OC2B/INT1)_PD3)
MISO: ICSP.MISO (1), J1.6 (MISO), U4.16 ((PCINT4/MISO)_PB4)
MOSI: ICSP.MOSI (4), J1.7 (MOSI), U4.15 ((PCINT3/OC2A/MOSI)_PB3)
unnamed: J3.1, R8.1
unnamed: D1.C, R4.1
unnamed: D3.C, R6.1
unnamed: D2.C, R5.1
unnamed: D4.C, R2.1
unnamed: J4.1, R9.1
unnamed: J5.1, R10.1
unnamed: C4.1, U4.20 (AREF)
RADIO_RST: J1.9 (RST), U4.32 (PD2_(INT0/PCINT18))
RX: JP2.2, U4.30 (PD0_(RXD/PCINT16))
SCK: ICSP.SCK (3), J1.5 (SCK), U4.17 (PB5_(SCK/PCINT5))
TX: JP2.1, U4.31 (PD1_(TXD/PCINT17))
WIRELESS_LED: D2.A, U2.16 (B1), U4.9 ((PCINT21/OC0B/T1)_PD5)
WIRELESS_LED_CONN: R9.2, U2.1 (A1)

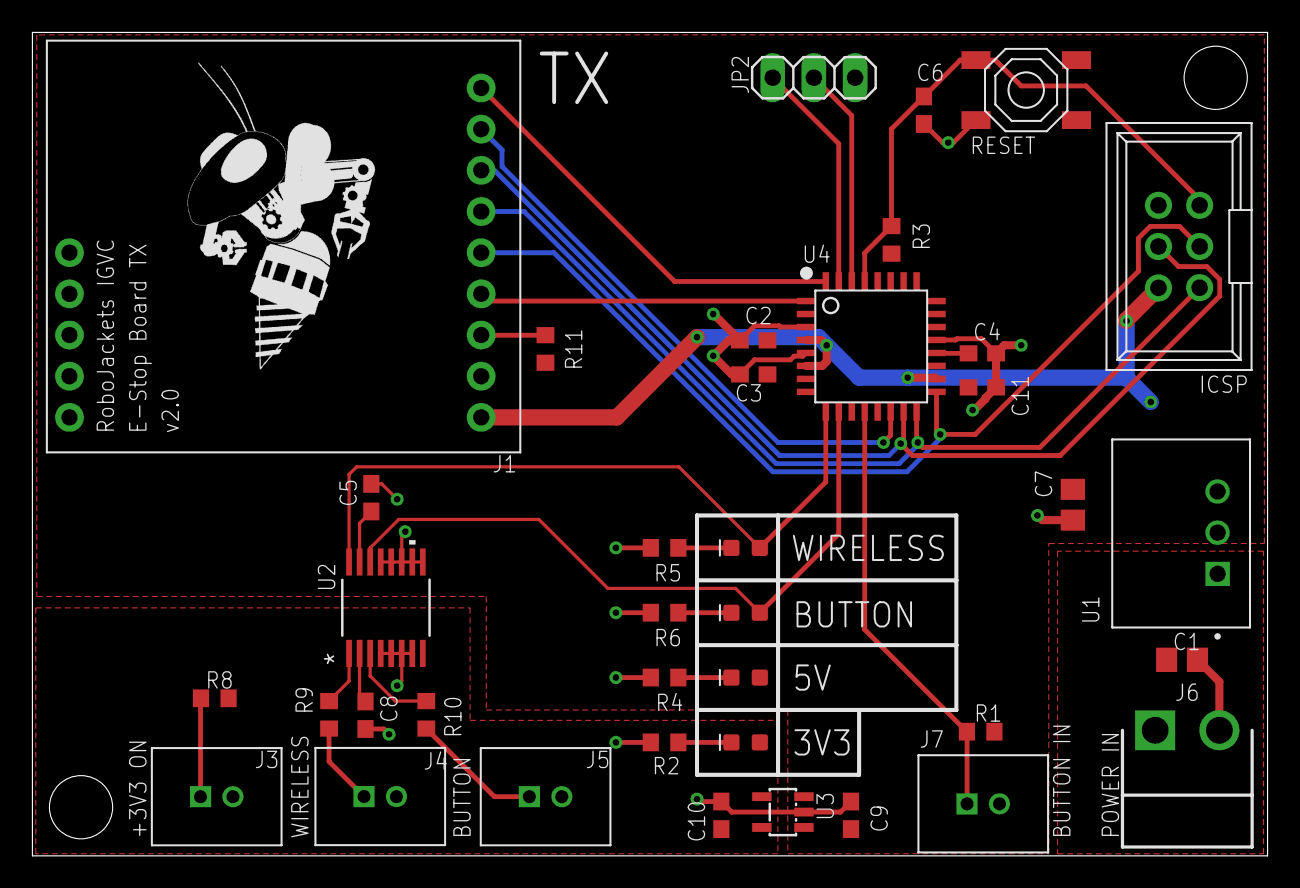
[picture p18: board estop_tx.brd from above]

Board: 2 copper layers, 76.2 x 50.8 mm, 41 parts (0 on the bottom side), 27 nets.

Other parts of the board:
U$1: ROBOBUZZ_1.0X
U$2, U$3: STANDOFF-HOLE

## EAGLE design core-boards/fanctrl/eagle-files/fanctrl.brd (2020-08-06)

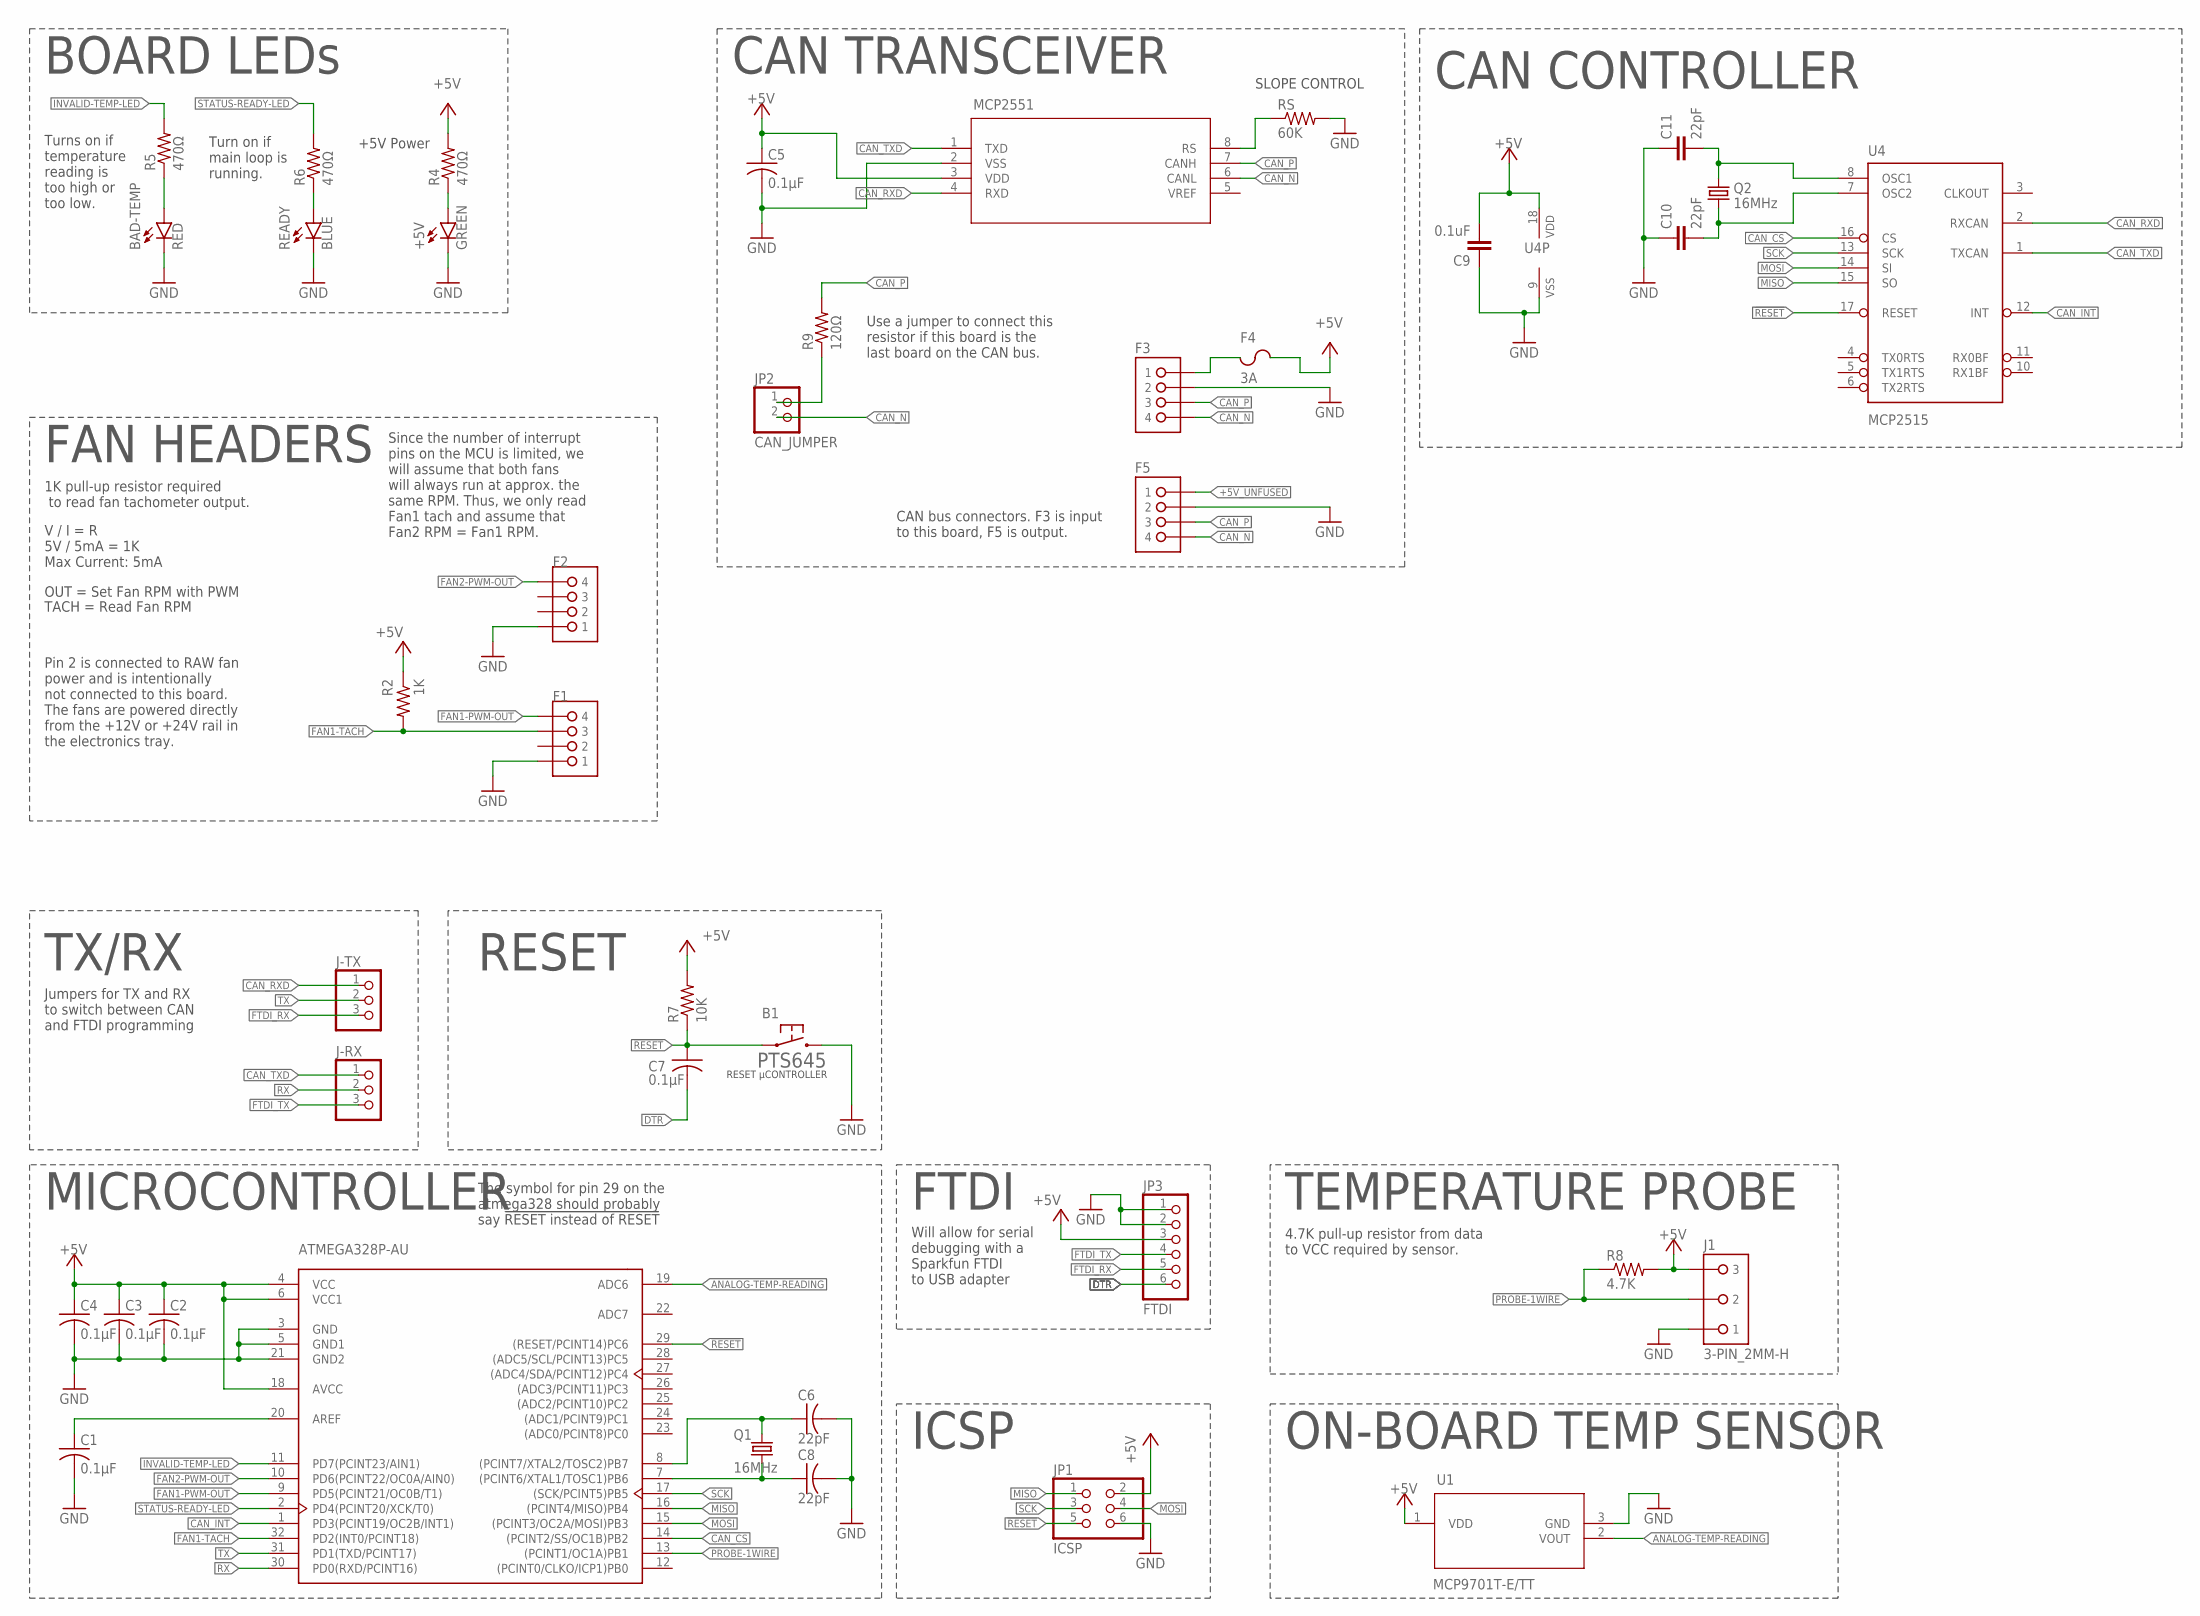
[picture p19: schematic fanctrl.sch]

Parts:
+5V: GREEN; CHIPLED_0603
ATMEGA328: ATMEGA328P-AU; TQFP-32
B1: PTS645
BAD-TEMP: RED; CHIPLED_0603
C1, C2, C3, C4, C5, C7: 0.1µF; C0603
C6, C8: 22pF; C0603
C9: 0.1uF; 0603-CAP
C10, C11: 22pF; 0603-CAP
F1, F2, F3, F5: 4-PIN_2MM-H; 2MM-4-H
F4: 3A; F1206
J1: 3-PIN_2MM-H; 2MM-3-H
J-RX: PINHD-1X3; 1X03
J-TX: PINHD-1X3; 1X03
JP1: ICSP; 2X03
JP2: CAN_JUMPER; 1X02
JP3: FTDI; 1X06/90
MCP2551: MCP2551T-I/SN; SOIC8-N_MC
Q1, Q2: 16MHz; CRYSTAL-SMD-5X3
R2: 1K; R0603
R4, R5, R6: 470Ω; R0603
R7: 10K; R0603
R8: 4.7K; R0603
R9: 120Ω; R0603
READY: BLUE; CHIPLED_0603
RS: 60K; R0603
U1: MCP9701T-E/TT; SOT-23_MC
U4: MCP2515; SO-18W

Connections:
!RESET: ATMEGA328.29 ((RESET/PCINT14)PC6), B1.P$1 (1), B1.P$2 (1), C7.1, JP1.5, R7.1, U4.17 (RESET)
+5V: ATMEGA328.4 (VCC), ATMEGA328.6 (VCC1), ATMEGA328.18 (AVCC), C2.1, C3.1, C4.1, C5.1, C9.2, F4.2, JP1.2, JP3.3, MCP2551.3 (VDD), R2.1, R4.2, R7.2, U1.1 (VDD), U4.18 (VDD)
+5V_UNFUSED: F3.1, F4.1, F5.1
ANALOG-TEMP-READING: ATMEGA328.19 (ADC6), U1.2 (VOUT)
AREF: ATMEGA328.20 (AREF), C1.1
CAN_CS: ATMEGA328.14 ((PCINT2/SS/OC1B)PB2), U4.16 (CS)
CAN_INT: ATMEGA328.1 (PD3(PCINT19/OC2B/INT1)), U4.12 (INT)
CAN_N: F3.4, F5.4, JP2.2, MCP2551.6 (CANL)
CAN_P: F3.3, F5.3, MCP2551.7 (CANH), R9.2
CAN_RS: MCP2551.8 (RS), RS.1
CAN_RXD: J-TX.1, MCP2551.4 (RXD), U4.2 (RXCAN)
CAN_TXD: J-RX.1, MCP2551.1 (TXD), U4.1 (TXCAN)
DTR: C7.2, JP3.6
FAN1-PWM-OUT: ATMEGA328.9 (PD5(PCINT21/OC0B/T1)), F1.4
FAN1-TACH: ATMEGA328.32 (PD2(INT0/PCINT18)), F1.3, R2.2
FAN2-PWM-OUT: ATMEGA328.10 (PD6(PCINT22/OC0A/AIN0)), F2.4
FTDI_RX: J-TX.3, JP3.5
FTDI_TX: J-RX.3, JP3.4
GND: +5V.C, ATMEGA328.3 (GND), ATMEGA328.5 (GND1), ATMEGA328.21 (GND2), B1.P$3 (2), B1.P$4 (2), BAD-TEMP.C, C1.2, C2.2, C3.2, C4.2, C5.2, C6.2, C8.2, C9.1, C10.1, C11.1, F1.1, F2.1, F3.2, F5.2, J1.1, JP1.6, JP3.1, JP3.2, MCP2551.2 (VSS), READY.C, RS.2, U1.3 (GND), U4.9 (VSS)
INVALID-TEMP-LED: ATMEGA328.11 (PD7(PCINT23/AIN1)), R5.2
MISO: ATMEGA328.16 ((PCINT4/MISO)PB4), JP1.1, U4.15 (SO)
MOSI: ATMEGA328.15 ((PCINT3/OC2A/MOSI)PB3), JP1.4, U4.14 (SI)
unnamed: ATMEGA328.7 ((PCINT6/XTAL1/TOSC1)PB6), C8.1, Q1.1
unnamed: J1.3, R8.2
unnamed: +5V.A, R4.1
unnamed: BAD-TEMP.A, R5.1
unnamed: R6.1, READY.A
unnamed: ATMEGA328.8 ((PCINT7/XTAL2/TOSC2)PB7), C6.1, Q1.3 (2)
unnamed: C11.2, Q2.3 (2), U4.8 (OSC1)
unnamed: C10.2, Q2.1, U4.7 (OSC2)
PROBE-1WIRE: ATMEGA328.13 ((PCINT1/OC1A)PB1), J1.2, R8.1
RX: ATMEGA328.30 (PD0(RXD/PCINT16)), J-RX.2
R_JUMPER: JP2.1, R9.1
SCK: ATMEGA328.17 ((SCK/PCINT5)PB5), JP1.3, U4.13 (SCK)
STATUS-READY-LED: ATMEGA328.2 (PD4(PCINT20/XCK/T0)), R6.2
TX: ATMEGA328.31 (PD1(TXD/PCINT17)), J-TX.2

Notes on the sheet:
MICROCONTROLLER
BOARD LEDs
RESET
CAN TRANSCEIVER
FAN HEADERS
TEMPERATURE PROBE
ON-BOARD TEMP SENSOR
4.7K pull-up resistor from data to VCC required by sensor.
1K pull-up resistor required to read fan tachometer output.
The symbol for pin 29 on the atmega328 should probably say !RESET instead of RESET
V / I = R 5V / 5mA = 1K Max Current: 5mA
ICSP
OUT = Set Fan RPM with PWM
TACH = Read Fan RPM
Use a jumper to connect this resistor if this board is the last board on the CAN bus.
CAN bus connectors. F3 is input to this board, F5 is output.
Pin 2 is connected to RAW fan power and is intentionally not connected to this board. The fans are powered directly from the +12V or +24V rail in the electronics tray.
+5V Power
Turns on if temperature reading is too high or too low.
Turn on if main loop is running.
FTDI
SLOPE CONTROL
TX/RX
CAN CONTROLLER
Jumpers for TX and RX to switch between CAN and FTDI programming
Will allow for serial debugging with a Sparkfun FTDI to USB adapter
Since the number of interrupt pins on the MCU is limited, we will assume that both fans will always run at approx. the same RPM. Thus, we only read Fan1 tach and assume that Fan2 RPM = Fan1 RPM.

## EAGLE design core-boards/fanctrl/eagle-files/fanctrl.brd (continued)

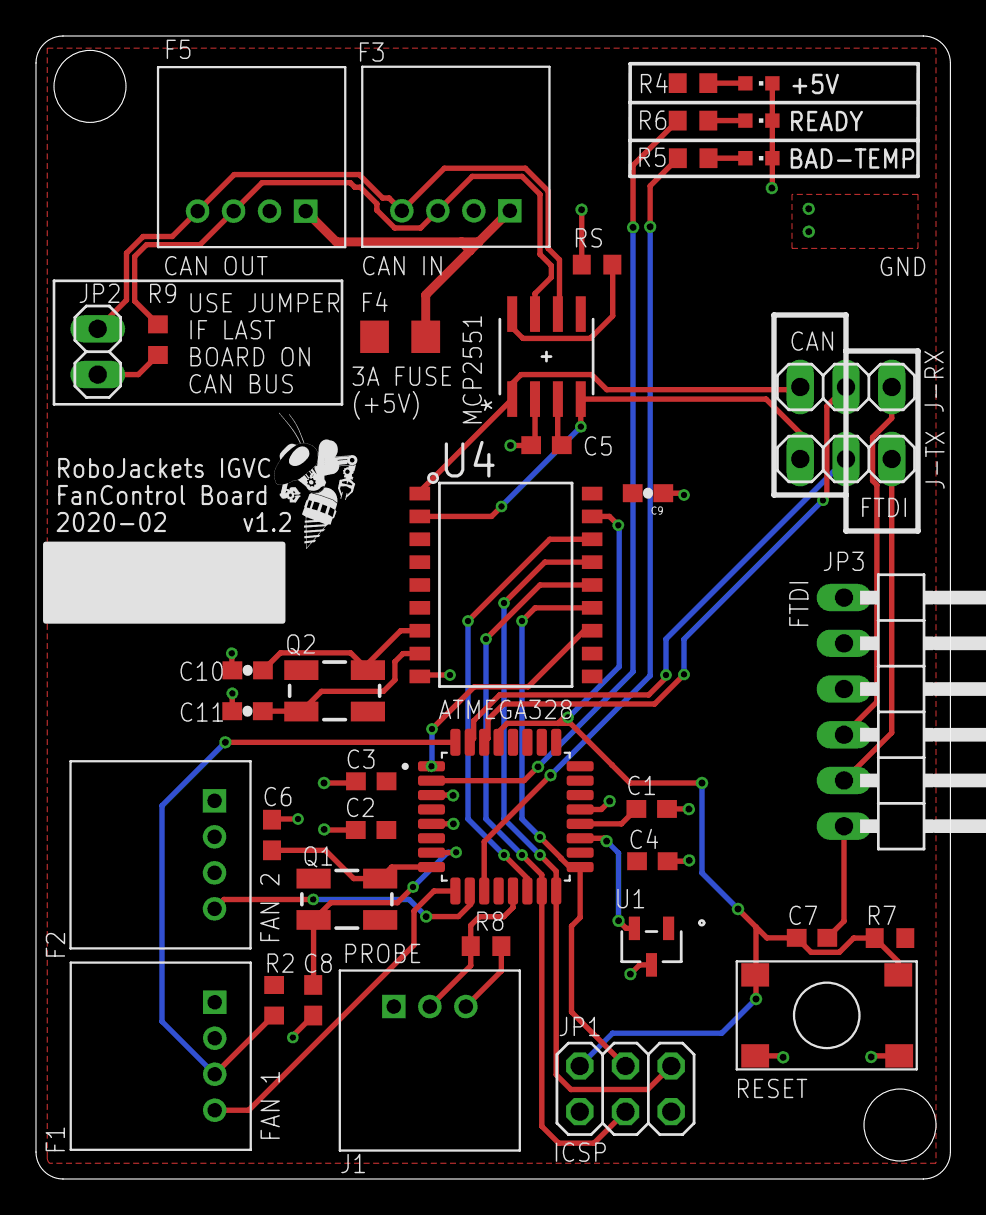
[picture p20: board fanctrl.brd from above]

Board: 2 copper layers, 50.8 x 63.5 mm, 41 parts (0 on the bottom side), 36 nets.

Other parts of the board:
U$1: ROBOBUZZ_0.4X

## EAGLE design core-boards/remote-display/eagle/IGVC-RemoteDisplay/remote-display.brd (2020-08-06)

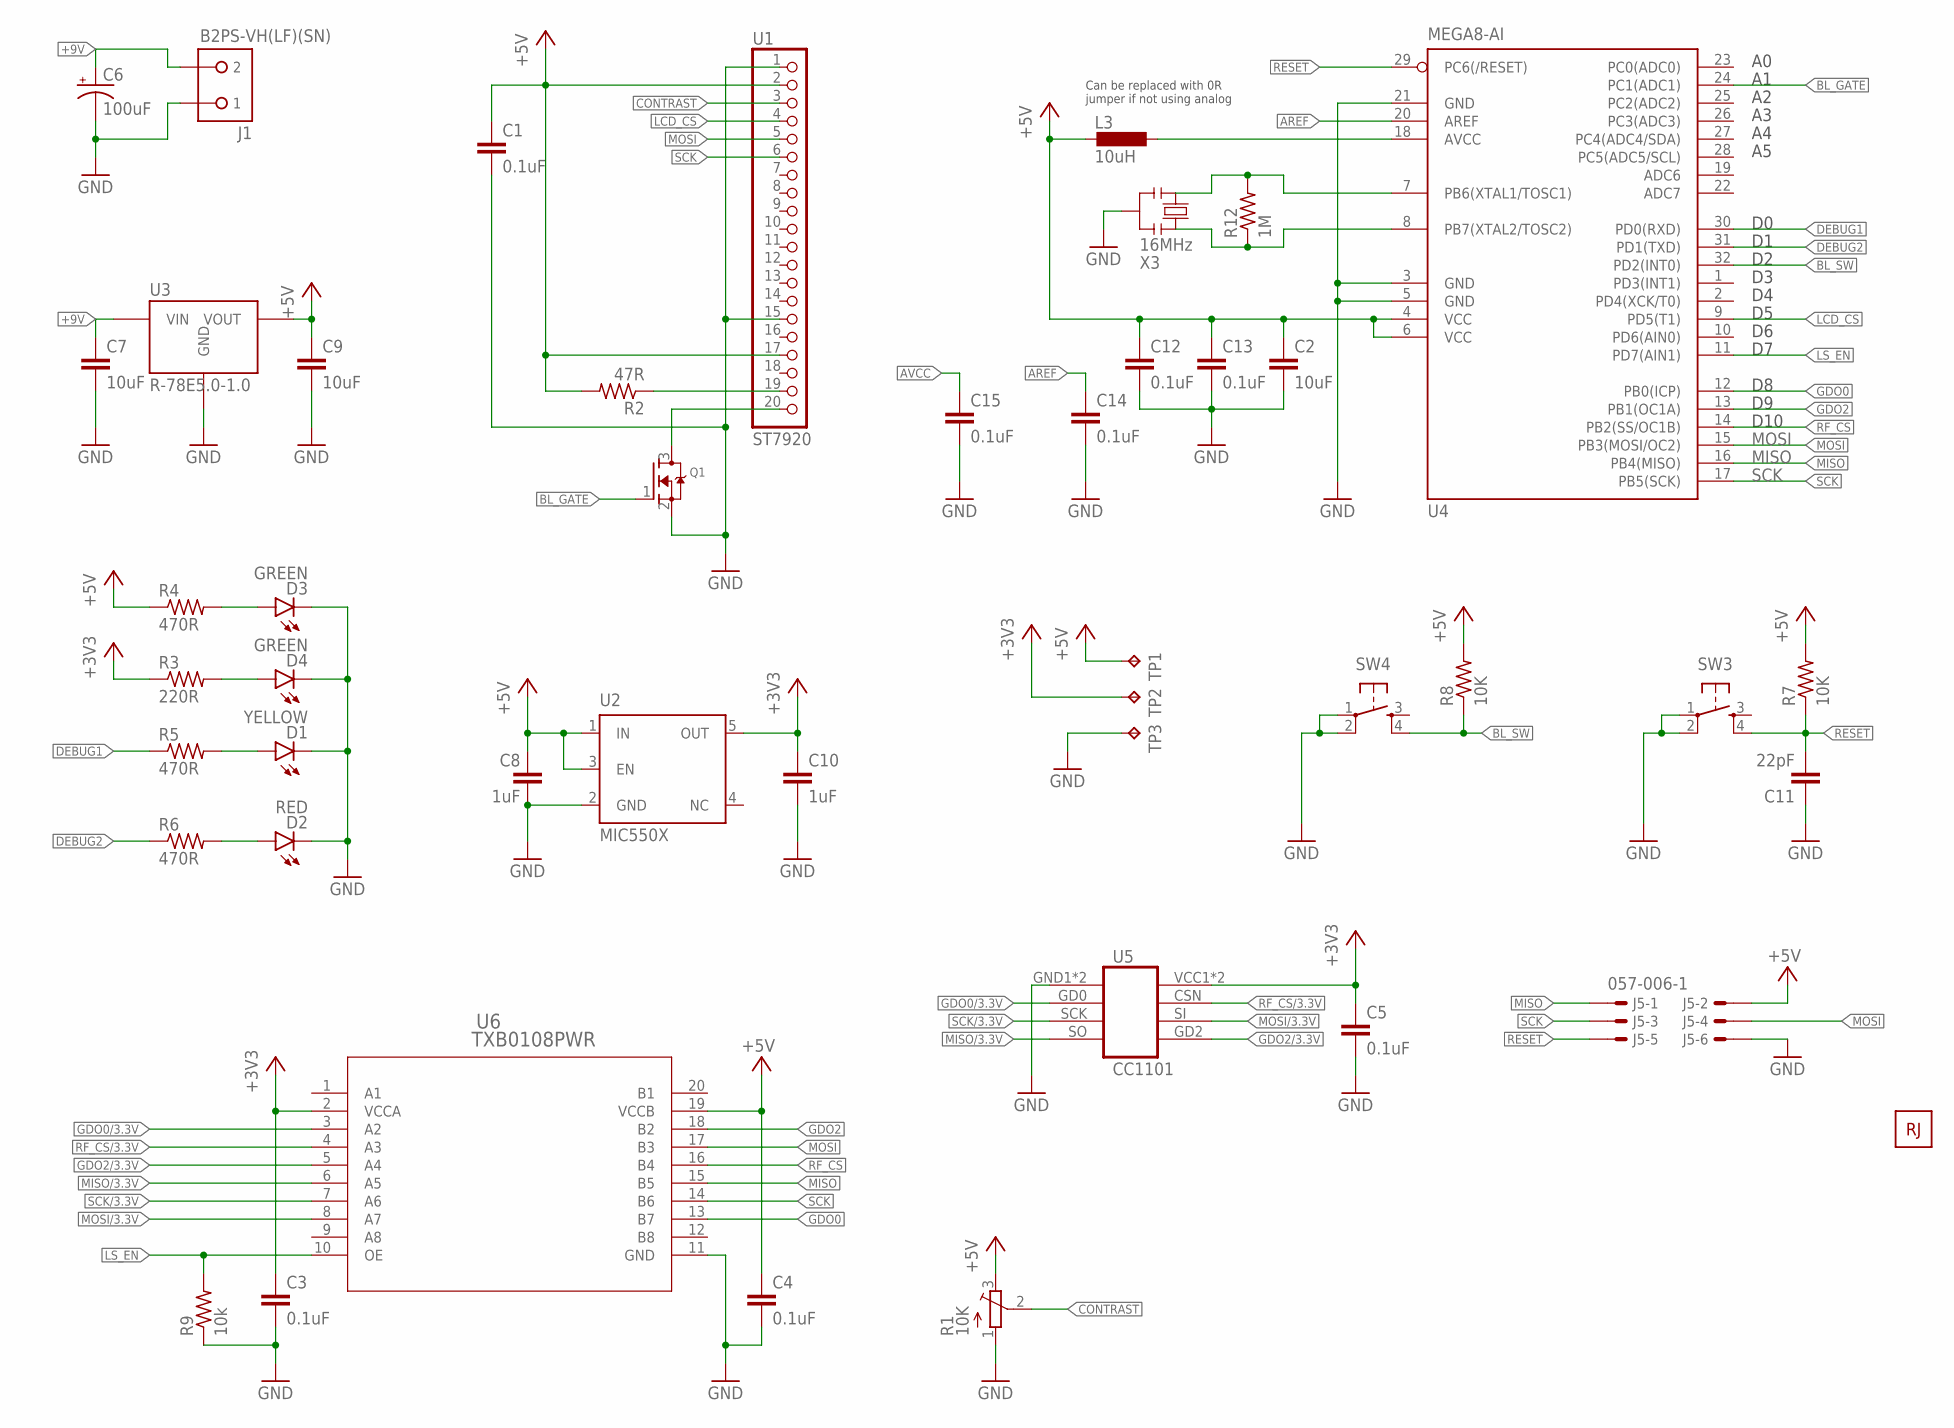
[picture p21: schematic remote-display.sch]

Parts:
C1, C3, C4, C5, C12, C13, C14, C15: 0.1uF; C0603
C2: 10uF; C0805
C6: 100uF; E5-10,5
C7, C9: 10uF; C0603
C8, C10: 1uF; C0603
C11: 22pF; C0603
D1: YELLOW; LED3MM
D2: RED; LED3MM
D3, D4: GREEN; LED3MM
J1: B2PS-VH(LF)(SN); B2PS-CENTERED
J5: 057-006-1; DIGIKEY 3M15451-ND
L3: 10uH; 0805
Q1: MOSFET-NREFLOW; SOT23
R1: 10K; TRIM-3386
R2: 47R; R0805
R3: 220R; R0603
R4, R5, R6: 470R; R0603
R7, R8: 10K; R0603
R9: 10k; R0603
R12: 1M; R0603
SW3, SW4: TL1105_A-H
TP1, TP2, TP3: TPPAD1-17; P1-17
U1: ST7920; ST7920-LCD
U2: MIC550X; SOT23-DBV
U3: R-78E5.0-1.0; R-78E
U4: MEGA8-AI; TQFP32-08
U5: CC1101; TI-CC1101
U6: TXB0108PWR; PW20
U$2: ROBOBUZZ1.0X; ROBOBUZZ_1.0X
X3: 16MHz; RESONATOR

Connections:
!RESET: C11.2, J5.5, R7.1, SW3.4, U4.29 (PC6(/RESET))
!RF_CS!: U4.14 (PB2(SS/OC1B)), U6.16 (B4)
!RF_CS!/3.3V: U5.CSN, U6.4 (A3)
+3V3: C3.1, C5.1, C10.1, R3.1, TP2.TP, U2.5 (OUT), U5.VCC1 (VCC), U5.VCC2 (VCC), U6.2 (VCCA)
+5V: C1.1, C2.1, C4.1, C8.1, C9.1, C12.1, C13.1, J5.2, L3.2, R1.3 (E), R2.2, R4.1, R7.2, R8.2, TP1.TP, U1.2, U1.17, U2.1 (IN), U2.3 (EN), U3.3 (VOUT), U4.4 (VCC), U4.6 (VCC), U6.19 (VCCB)
+9V: C6.+, C7.1, J1.2, U3.1 (VIN)
AREF: C14.1, U4.20 (AREF)
AVCC: C15.1, L3.1, U4.18 (AVCC)
BL_DRAIN: Q1.3 (D), U1.20
BL_GATE: Q1.1 (G), U4.24 (PC1(ADC1))
BL_SW: R8.1, SW4.4, U4.32 (PD2(INT0))
CONTRAST: R1.2 (S), U1.3
DEBUG1: R5.1, U4.30 (PD0(RXD))
DEBUG2: R6.1, U4.31 (PD1(TXD))
GDO0: U4.12 (PB0(ICP)), U6.13 (B7)
GDO0/3.3V: U5.GD0 (CE), U6.3 (A2)
GDO2: U4.13 (PB1(OC1A)), U6.18 (B2)
GDO2/3.3V: U5.GD2 (IRQ), U6.5 (A4)
GND: C1.2, C2.2, C3.2, C4.2, C5.2, C6.-, C7.2, C8.2, C9.2, C10.2, C11.1, C12.2, C13.2, C14.2, C15.2, D1.K (C), D2.K (C), D3.K (C), D4.K (C), J1.1, J5.6, Q1.2 (S), R1.1 (A), R9.1, SW3.1, SW3.2, SW4.1, SW4.2, TP3.TP, U1.1, U1.15, U2.2 (GND), U3.2 (GND), U4.3 (GND), U4.5 (GND), U4.21 (GND), U5.GND1 (GND), U5.GND2 (GND), U6.11 (GND), X3.2
LCD_BL: R2.1, U1.19
LCD_CS: U1.4, U4.9 (PD5(T1))
LS_EN: R9.2, U4.11 (PD7(AIN1)), U6.10 (OE)
MISO: J5.1, U4.16 (PB4(MISO)), U6.15 (B5)
MISO/3.3V: U5.SO (MISO), U6.6 (A5)
MOSI: J5.4, U1.5, U4.15 (PB3(MOSI/OC2)), U6.17 (B3)
MOSI/3.3V: U5.SI (MOSI), U6.8 (A7)
PWR_LED: D3.A, R4.2
PWR_LED1: D4.A, R3.2
SCK: J5.3, U1.6, U4.17 (PB5(SCK)), U6.14 (B6)
SCK/3.3V: U5.SCK, U6.7 (A6)
STAT1_LED: D1.A, R5.2
STAT2_LED: D2.A, R6.2
XTAL1: R12.2, U4.7 (PB6(XTAL1/TOSC1)), X3.1
XTAL2: R12.1, U4.8 (PB7(XTAL2/TOSC2)), X3.3

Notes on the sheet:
D10
Can be replaced with 0R jumper if not using analog

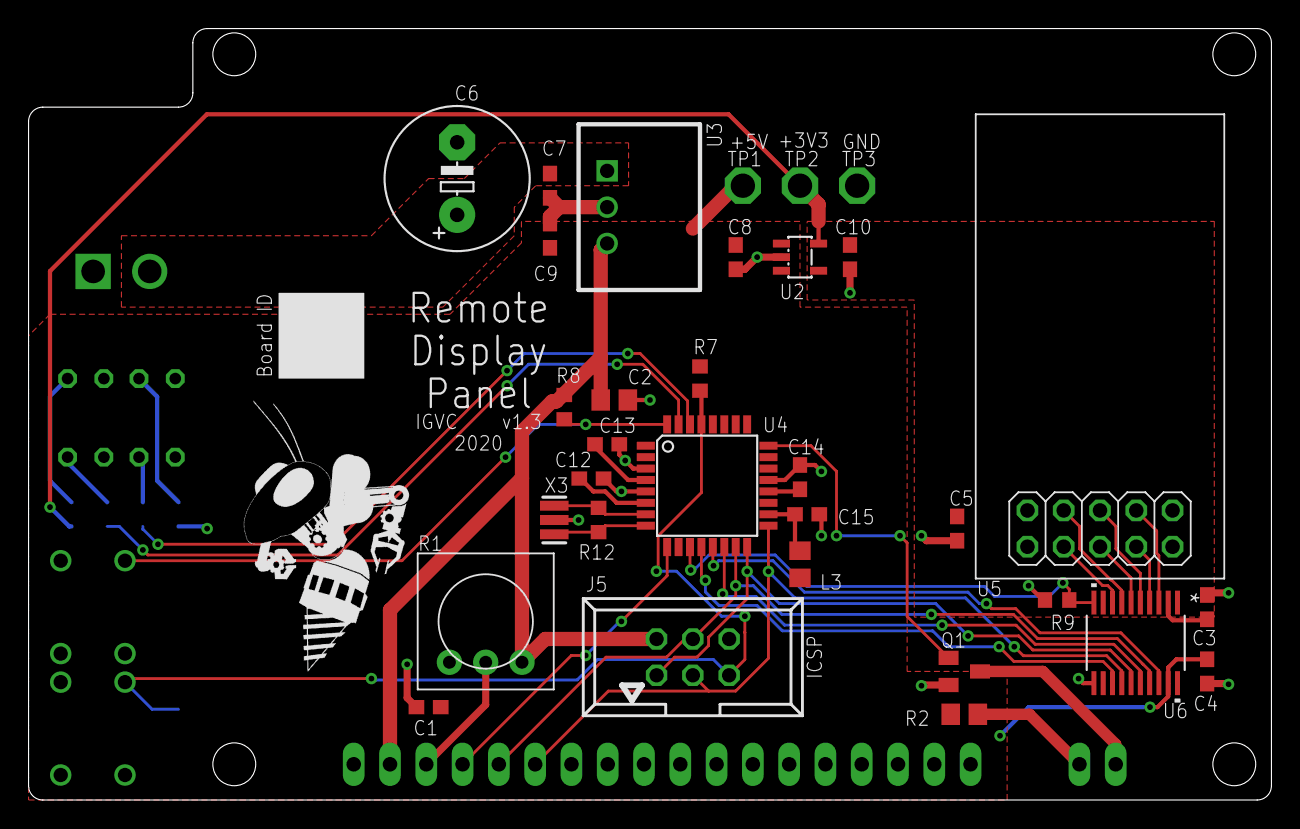
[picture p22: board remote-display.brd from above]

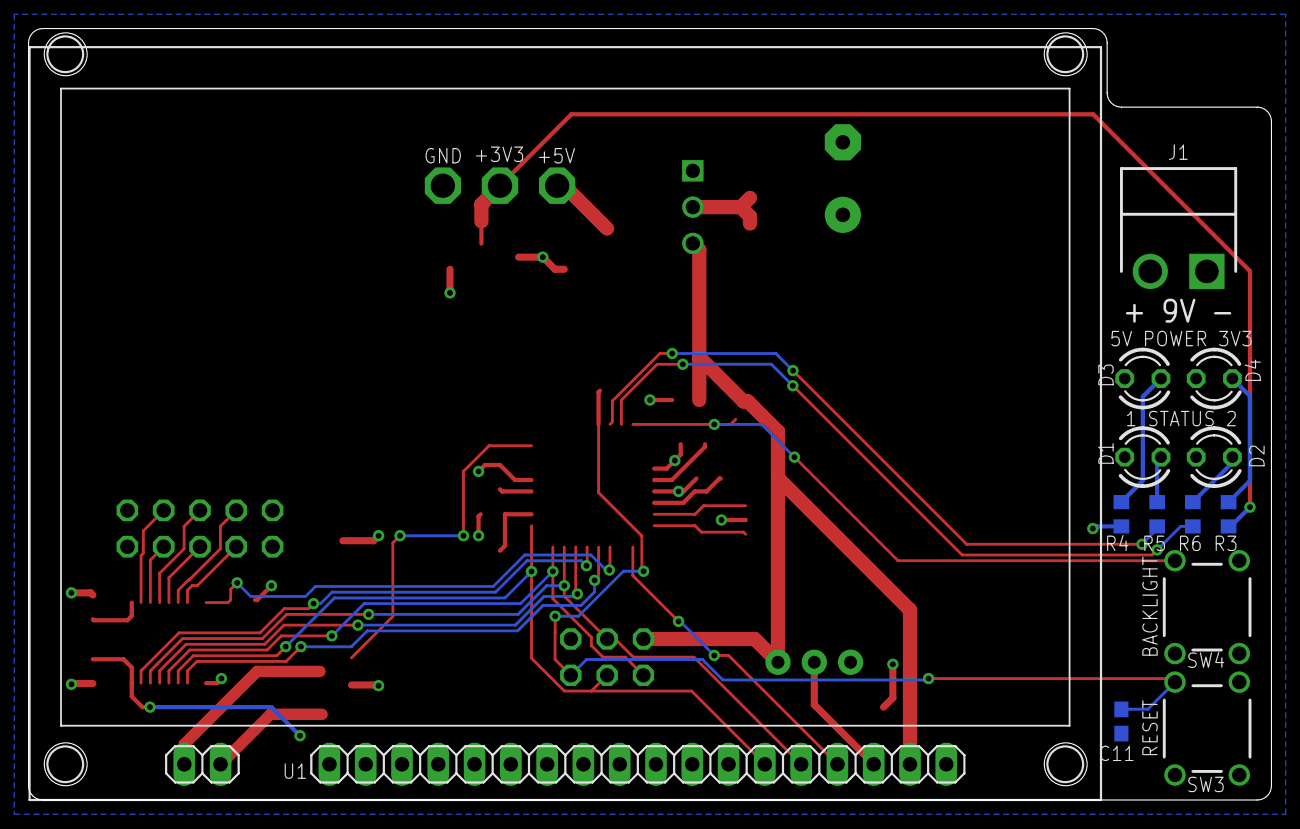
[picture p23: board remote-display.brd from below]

Board: 2 copper layers, 87.0 x 54.0 mm, 46 parts (13 on the bottom side), 34 nets.

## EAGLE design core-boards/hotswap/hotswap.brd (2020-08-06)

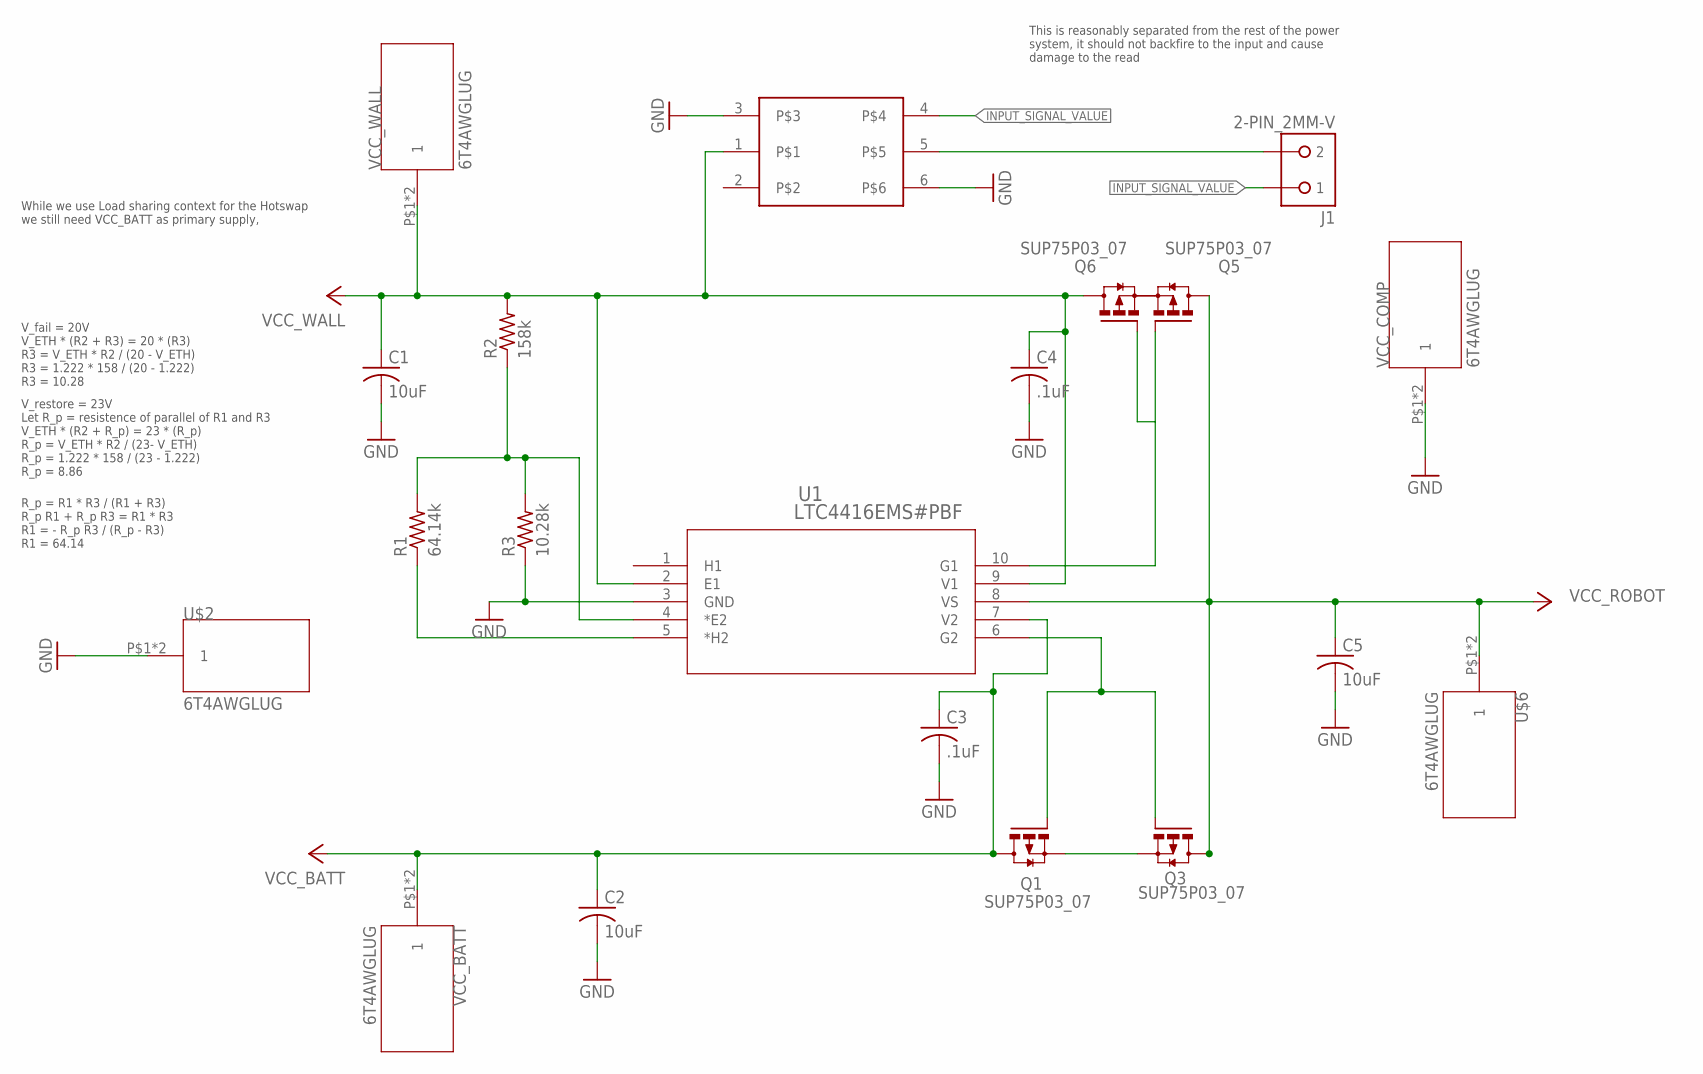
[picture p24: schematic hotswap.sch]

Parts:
C1, C2, C5: 10uF; C1210
C3, C4: .1uF; C0805
J1: 2-PIN_2MM-V; 2MM-2-V
Q1, Q3, Q5, Q6: SUP75P03_07; DPACK_2
R1: 64.14k; R0603
R2: 158k; R0603
R3: 10.28k; R0603
U1: LTC4416EMS#PBF; MSOP-10_MS
U$2, U$6: 6T4AWGLUG
VCC_BATT: 6T4AWGLUG
VCC_COMP: 6T4AWGLUG
VCC_WALL: 6T4AWGLUG
Z1: TLP2745

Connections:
GND: C1.2, C2.2, C3.2, C4.2, C5.2, R3.1, U1.3 (GND), U$2.P$1, U$2.P$2, VCC_COMP.P$1, VCC_COMP.P$2, Z1.3, Z1.6
INPUT_SIGNAL_VALUE: J1.1, Z1.4
unnamed: Q1.S, Q3.S
unnamed: Q1.G, Q3.G, U1.6 (G2)
unnamed: Q5.G, Q6.G, U1.10 (G1)
unnamed: R1.2, R2.1, R3.2, U1.4 (*E2)
unnamed: J1.2, Z1.5
unnamed: R1.1, U1.5 (*H2)
VCC_BATT: C2.1, C3.1, Q1.D, U1.7 (V2), VCC_BATT.P$1, VCC_BATT.P$2
VCC_ROBOT: C5.1, Q3.D, Q5.D, U1.8 (VS), U$6.P$1, U$6.P$2
VCC_WALL: C1.1, C4.1, Q6.D, R2.2, U1.2 (E1), U1.9 (V1), VCC_WALL.P$1, VCC_WALL.P$2, Z1.1

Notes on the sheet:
This is reasonably separated from the rest of the power system, it should not backfire to the input and cause damage to the read
While we use Load sharing context for the Hotswap we still need VCC_BATT as primary supply,
V_fail = 20V V_ETH * (R2 + R3) = 20 * (R3) R3 = V_ETH * R2 / (20 - V_ETH) R3 = 1.222 * 158 / (20 - 1.222) R3 = 10.28
V_restore = 23V Let R_p = resistence of parallel of R1 and R3 V_ETH * (R2 + R_p) = 23 * (R_p) R_p = V_ETH * R2 / (23- V_ETH) R_p = 1.222 * 158 / (23 - 1.222) R_p = 8.86
R_p = R1 * R3 / (R1 + R3) R_p R1 + R_p R3 = R1 * R3 R1 = - R_p R3 / (R_p - R3) R1 = 64.14


Board: 2 copper layers, 92.8 x 57.1 mm, 25 parts (1 on the bottom side), 11 nets.

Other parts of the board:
E$1: ROBOBUZZ_0.8X
U$3, U$4, U$5, U$7: STANDOFF-HOLE

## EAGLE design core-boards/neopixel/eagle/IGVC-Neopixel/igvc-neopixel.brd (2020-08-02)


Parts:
+5V_ON: GREEN; CHIP-LED0805; DIGIKEY 732-4982-1-ND
C1: 0.01uF; C0603; DIGIKEY 311-1572-1-ND
C2, C3: 4.7uF; C1206; DIGIKEY 1276-3178-1-ND
C4, C5: 47uF; E5-10,5; DIGIKEY PCE3753CT-ND
C6: 1000u 6.3V; E5-10,5; DIGIKEY 493-2160-1-ND
C7, C8, C12, C13, C14: 0.1uF; C0603; DIGIKEY 399-1099-1-ND
C11: 22pF; C0603; DIGIKEY 311-3952-1-ND
C15: 0.1uF; C0603
C16, C17: 22pF; C0603; DIGIKEY 399-1099-1-ND
D1: B550C; SMC; DIGIKEY B550C-FDICT-ND
DEBUG1, DEBUG2: YELLOW; CHIP-LED0805; DIGIKEY 732-4987-1-ND
IC1: RT8289; SOIC8_EP; DIGIKEY 1028-1046-1-ND
IC3: MCP2551T-I/SN; SOIC8-N_MC; DIGIKEY MCP2551T-I/SNCT-ND
IC4: MEGA8-AI; TQFP32-08; DIGIKEY ATMEGA328P-AURCT-ND
J1: B2PS-VH(LF)(SN); B2PS-CENTERED
J2, J4: 4-PIN_2MM-H; 2MM-4-H
J3: S3B-VH; DIGIKEY 455-1649-ND
J5: 057-006-1; DIGIKEY 3M15451-ND
L1: 10uH; SRR1208; DIGIKEY SRR1208-100MLCT-ND
L3: 10uH; 0805; DIGIKEY 490-1053-1-ND
R1, R4: 10k; R0603; DIGIKEY RNCP0603FTD10K0CT-ND
R2: 3.16k; R0603; DIGIKEY RMCF0603FT3K16CT-ND
R3, R6, R8: 470R; R0603; DIGIKEY RMCF0603JT470RCT-ND
R5: 10k; R0603
R7: 330R; R0603; DIGIKEY RMCF0603JT330RCT-ND
R9: 120R; R0603; DIGIKEY RMCF0603JT120RCT-ND
R12: 1M; R0603; DIGIKEY 311-1.00MHRCT-ND
SW1: SPST_TACT-EVQQ2; EVQ-Q2; DIGIKEY P12961SCT-ND
U4: MCP2515; SO-18W
U$1: ROBOBUZZ0.6X; ROBOBUZZ_0.6X
X2: 16MHz; CRYSTAL-SMD-5X3
X3: 16MHz; RESONATOR; DIGIKEY 490-17948-1-ND

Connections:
!RESET: C11.2, IC4.29 (PC6(/RESET)), J5.5, R4.1, SW1.B (S), SW1.B' (S1), U4.17 (RESET)
+5V: C4.+, C5.+, C6.+, C7.1, C8.1, C12.1, C15.1, IC3.3 (VDD), IC4.4 (VCC), IC4.6 (VCC), J3.1 (X-1), J5.2, L1.2, L3.2, R1.2, R3.1, R4.2, R5.2, U4.18 (VDD)
+12V: C2.1, C3.1, IC1.7 (VIN), J1.2
AREF: C13.1, IC4.20 (AREF)
AVCC: C14.1, IC4.18 (AVCC), L3.1
BOOT: C1.1, IC1.1 (BOOT)
CAN_5V: J2.1, J4.1
CAN_CS: IC4.14 (PB2(SS/OC1B)), R5.1, U4.16 (CS)
CAN_INT: IC4.32 (PD2(INT0)), U4.12 (INT)
CAN_N: IC3.6 (CANL), J2.4, J4.4, R9.1
CAN_P: IC3.7 (CANH), J2.3, J4.3, R9.2
CAN_RXD: IC3.1 (TXD), U4.2 (RXCAN)
CAN_TXD: IC3.4 (RXD), U4.1 (TXCAN)
DBG1: IC4.25 (PC2(ADC2)), R6.1
DBG2: IC4.26 (PC3(ADC3)), R8.1
FB: IC1.4 (FB), R1.1, R2.2
GND: +5V_ON.C, C2.2, C3.2, C4.-, C5.-, C6.-, C7.2, C8.2, C11.1, C12.2, C13.2, C14.2, C15.2, C16.1, C17.1, D1.A, DEBUG1.C, DEBUG2.C, IC1.6 (GND), IC1.EXP (GND), IC3.2 (VSS), IC3.8 (RS), IC4.3 (GND), IC4.5 (GND), IC4.21 (GND), J1.1, J2.2, J3.3 (X-3), J4.2, J5.6, R2.1, SW1.A, SW1.A' (P1), U4.9 (VSS), X3.2
LED_DATA: IC4.24 (PC1(ADC1)), R7.1
MISO: IC4.16 (PB4(MISO)), J5.1, U4.15 (SO)
MOSI: IC4.15 (PB3(MOSI/OC2)), J5.4, U4.14 (SI)
unnamed: C17.2, U4.8 (OSC1), X2.3 (2)
unnamed: C16.2, U4.7 (OSC2), X2.1
NEOPIXEL: J3.2 (X-2), R7.2
PWR_LED: +5V_ON.A, R3.2
SCK: IC4.17 (PB5(SCK)), J5.3, U4.13 (SCK)
STAT1_LED: DEBUG1.A, R6.2
STAT2_LED: DEBUG2.A, R8.2
SW: C1.2, D1.C, IC1.8 (SW), L1.1
XTAL1: IC4.7 (PB6(XTAL1/TOSC1)), R12.2, X3.1
XTAL2: IC4.8 (PB7(XTAL2/TOSC2)), R12.1, X3.3

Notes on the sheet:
D10
Max. Current = 5A
From Neopixel Best Practices: "Before connecting NeoPixels to any large power source (DC “wall wart” or even a large battery), add a capacitor (1000 µF, 6.3V or higher) across the + and – terminals as shown above. The capacitor buffers sudden changes in the current drawn by the strip."
For automatic startup, leave EN unconnected.


Board: 2 copper layers, 50.8 x 63.5 mm, 44 parts (0 on the bottom side), 30 nets.

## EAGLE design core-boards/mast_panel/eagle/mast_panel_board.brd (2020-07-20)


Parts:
C1, C4: 22pF; 0603-CAP
C2, C3: 10uF; C0805
C5, C6: 1uF; C0603
C7, C8, C9: 0.1uF; C0402
D2: GREEN; CHIP-LED0603
D3: BLUE; CHIP-LED0603
J1: 2-PIN_2MM-V; 2MM-2-V
J4: 4-PIN_2MM-H; 2MM-4-H
JP1, JP2, JP3: PINHD-1X14; 1X14
PROG: ICSP Connector; 2X3SHROUDED
Q1: 16MHz; CRYSTAL-SMD-5X3
R1, R2: 20kOh; R0603
R3: 10kO; R0603
R4: 120; R0603
R5, R6, R7, R8, R9, R10: 50kO; R0805
R11, R12: 780; R0402
S3: SKQGADE010; SW4-SMD-5.2X5.2X1.5MM
TP1, TP2: TEST-POINT3X5; PAD.03X.05
U1: ATMEGA328P-AUR; 32A
U3: MCP2551T-I/SN; SOIC8-N_MC
U4: MCP2515; SO-18W

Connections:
+5V: C2.1, C3.1, C5.1, C6.1, C7.1, C8.1, C9.1, J4.1, JP1.2, JP1.13, JP2.2, JP2.13, JP3.1, PROG.+5V (2), R3.2, R11.2, U1.4 (VCC_2), U1.6 (VCC), U1.18 (AVCC), U3.3 (VDD)
BUTTON: JP3.2, U1.23 (PC0_(ADC0/PCINT8))
CAN_N: J1.2, J4.4, U3.6 (CANL)
CAN_P: J4.3, R4.2, U3.7 (CANH)
CAN_SS: U1.31 (PD1_(TXD/PCINT17)), U4.16 (CS)
GND: C1.1, C2.2, C3.2, C4.1, C5.2, C6.2, C7.2, C8.2, C9.2, D2.C (K), D3.C (K), J4.2, JP1.1, JP1.14, JP2.1, JP2.14, JP3.4, JP3.6, JP3.8, JP3.10, JP3.12, JP3.14, PROG.GND (6), S3.4 (B0), U1.3 (GND_2), U1.5 (GND_3), U1.21 (GND), U3.2 (VSS), U3.8 (RS)
LCD1_RST: JP1.11, U1.13 ((PCINT1/OC1A)_PB1)
LCD1_SS: JP1.4, U1.14 ((PCINT2/SS/OC1B)_PB2)
LCD1_V0: JP1.3, R2.2
LCD2_RST: JP2.11, U1.9 ((PCINT21/OC0B/T1)_PD5)
LCD2_SS: JP2.4, U1.12 ((PCINT0/CLKO/ICP1)_PB0)
LCD2_V0: JP2.3, R1.2
LCD_MOSI: JP1.5, JP2.5, PROG.MOSI (4), U1.15 ((PCINT3/OC2A/MOSI)_PB3), U4.14 (SI)
LCD_SCLK: JP1.6, JP2.6, PROG.SCK (3), U1.17 (PB5_(SCK/PCINT5)), U4.13 (SCK)
LED1: JP3.3, R5.1
LED2: JP3.5, R6.1
LED3: JP3.7, R7.1
LED4: JP3.9, R8.1
LED5: JP3.11, R9.1
LED6: JP3.13, R10.1
LED_CTRL1: R5.2, U1.24 (PC1_(ADC1/PCINT9))
LED_CTRL2: R6.2, U1.25 (PC2_(ADC2/PCINT10))
LED_CTRL3: R7.2, U1.26 (PC3_(ADC3/PCINT11))
LED_CTRL4: R8.2, U1.27 (PC4_(ADC4/SDA/PCINT12))
LED_CTRL5: R9.2, U1.28 (PC5_(ADC5/SCL/PCINT13))
LED_CTRL6: R10.2, U1.1 ((PCINT19/OC2B/INT1)_PD3)
MBED_CAN_INT: U1.32 (PD2_(INT0/PCINT18)), U4.12 (INT)
MBED_CAN_RD: TP2.P$1, U3.1 (TXD), U4.1 (TXCAN)
MBED_CAN_TD: TP1.P$1, U3.4 (RXD), U4.2 (RXCAN)
unnamed: J1.1, R4.1
unnamed: JP1.12, R2.1
unnamed: D2.A, R11.1
unnamed: D3.A, R12.1
unnamed: JP2.12, R1.1
unnamed: C4.2, Q1.3 (2), U4.8 (OSC1)
unnamed: C1.2, Q1.1, U4.7 (OSC2)
RESET: PROG.!RESET (5), R3.1, S3.1 (A0), U1.29 (PC6_(RESET/PCINT14)), U4.17 (RESET)
TEST_LED: PROG.MISO (1), R12.2, U1.16 ((PCINT4/MISO)_PB4), U4.15 (SO)
VDD: U4.18 (VDD)
VSS: U4.9 (VSS)


Board: 2 copper layers, 63.5 x 47.9 mm, 36 parts (0 on the bottom side), 38 nets.

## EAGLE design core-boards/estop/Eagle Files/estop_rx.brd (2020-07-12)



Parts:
C1, C5: 10uF; C0805
C2, C3, C4, C6, C7, C8: 0.1uF; C0603
C9, C10: 22pF; 0603-CAP
C11: 0.1uF; 0603-CAP
D1, D2, D3: Green; LED-0603
D12, D13, D14: S10M-TP; SMC
J1: RFM95W-3072
J2, J3: B2PS-VH(LF)(SN); B2PS-CENTERED
J4: 2-PIN_2MM-V; 2MM-2-V
J5: 6-PIN_2MM-V; 2MM-6-V
PROG: ICSP Connector; 2X3SHROUDED
Q1: BJT-NPN_; SOT-23-3
Q2: 16MHz; CRYSTAL-SMD-5X3
R1, R4, R5, R6: 1k; R0603
R2, R3, R7: 10k; R0603
R9: 4.7k; R0603
R10: 1.24k; R0603
RESET: SKQGADE010; SW4-SMD-5.2X5.2X1.5MM
U1: R-78E5.0-1.0CONV_R-78E5.0-1.0; CONV_R-78E5.0-1.0
U2: MCP2551T-E/SN; SOIC8-N_MC
U3: MCP2515; SO-18W
U4: ATMEGA328P-AUR
U6: D5V0L1B2WS-7; SOD323
U$1: G5LE-14

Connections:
!RESET: C6.1, PROG.!RESET (5), R2.1, RESET.1 (A0), U3.17 (RESET), U4.29 (PC6_(RESET/PCINT14))
+5V: C2.1, C3.1, C5.1, C7.1, C8.1, C11.2, D2.A, J1.1 (VCC), PROG.+5V (2), R2.2, R3.1, R7.1, U1.3 (OUT), U2.3 (VDD), U3.18 (VDD), U4.4 (VCC_2), U4.6 (VCC), U4.18 (AVCC), U$1.P$3 (TRIG2)
+12V: C1.1, J3.1, U1.1 (IN), U6.1 (EPAD_2)
+24V: D12.A, J5.1
BUTTON_LED: D1.A, U4.9 ((PCINT21/OC0B/T1)_PD5)
CAN_CS: R3.2, U3.16 (CS), U4.11 ((PCINT23/AIN1)_PD7)
CAN_INT: U3.12 (INT), U4.2 ((PCINT20/XCK/T0)_PD4)
CAN_N: J4.2, U2.6 (CANL)
CAN_P: J4.1, U2.7 (CANH)
CAN_RXD: U2.4 (RXD), U3.2 (RXCAN)
CAN_TXD: U2.1 (TXD), U3.1 (TXCAN)
CE: J1.8 (CS), U4.14 ((PCINT2/SS/OC1B)_PB2)
DIODE_TO_GREEN: D12.C, J5.2
DIODE_TO_INTER: D13.C, J5.4
ESTOP_IN: J2.1, R9.1, U$1.P$2 (OUT1)
ESTOP_MC_IN: R9.2, R10.1, U4.12 ((PCINT0/CLKO/ICP1)_PB0)
GND: C1.2, C2.2, C3.2, C4.2, C5.2, C6.2, C7.2, C8.2, C9.1, C10.1, C11.1, D14.A, J1.2 (GND), J2.2, J3.2, J5.6, PROG.GND (6), Q1.2 (E), R4.1, R5.1, R6.1, R10.2, RESET.4 (B0), U1.2 (GND), U2.2 (VSS), U2.8 (RS), U3.9 (VSS), U4.3 (GND_2), U4.5 (GND_3), U4.21 (GND), U6.2 (EPAD)
IRQ: J1.4 (IRQ), U4.1 ((PCINT19/OC2B/INT1)_PD3)
MISO: J1.6 (MISO), PROG.MISO (1), U3.15 (SO), U4.16 ((PCINT4/MISO)_PB4)
MOSI: J1.7 (MOSI), PROG.MOSI (4), U3.14 (SI), U4.15 ((PCINT3/OC2A/MOSI)_PB3)
MOTOR_POWER: D13.A, J5.3
unnamed: Q1.3 (C), U$1.P$1 (TRIG1)
unnamed: D2.C, R5.2
unnamed: D1.C, R4.2
unnamed: D3.C, R6.2
unnamed: Q1.1 (B), R1.2
unnamed: J1.3 (EN), R7.2
unnamed: C4.1, U4.20 (AREF)
unnamed: C10.2, Q2.3 (2), U3.8 (OSC1)
unnamed: C9.2, Q2.1, U3.7 (OSC2)
RADIO_RST: J1.9 (RST), U4.32 (PD2_(INT0/PCINT18))
RELAY_CTRL: R1.1, U4.13 ((PCINT1/OC1A)_PB1)
SCK: J1.5 (SCK), PROG.SCK (3), U3.13 (SCK), U4.17 (PB5_(SCK/PCINT5))
SOLENOID_TRIG: D14.C, J5.5, U$1.P$4 (IN)
WIRELESS_LED: D3.A, U4.10 ((PCINT22/OC0A/AIN0)_PD6)

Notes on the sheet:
Power
E-Stop Signal In
CAN Bus
CAN Controller


Board: 2 copper layers, 76.2 x 50.8 mm, 44 parts (1 on the bottom side), 35 nets.

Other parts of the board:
U$2: ROBOBUZZ_1.0X2
U$3, U$4: STANDOFF-HOLE

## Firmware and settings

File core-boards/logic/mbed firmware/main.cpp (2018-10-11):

#include "mbed.h"
#include "USBSerial.h"
#include <string>
#include <stdlib.h>
#define DEBUG false
#define TIMEOUT true

// Hardware definition
USBSerial serialNUC(0x1f00, 0x2012, 0x0001, true);
Timer timer;
Serial serial(p13, NC, 9600);

// mbed Pin definition
DigitalOut myLED1(LED1);
DigitalOut myLED2(LED2);
DigitalOut myLED3(LED3);
DigitalOut myLED4(LED4);
DigitalOut boardLED(p8);
DigitalOut eStopLight(p12);
DigitalIn eStopStatus(p18);

InterruptIn encoderLeftPinA(p28);
DigitalIn encoderLeftPinB(p27);
InterruptIn encoderRightPinA(p26);
DigitalIn encoderRightPinB(p25);
AnalogIn battery(p20);

// function prototypes
void parseCommand(char *);
void tickLeft();
void tickRight();
void pid();
void parseNonMotor(char *);
void setLeftSpeed(int);
void setRightSpeed(int);
void bothMotorStop();

// Serial Comm
long lastCmdTime = 0;
int lastLoopTime = 0;
uint8_t buffer[128];

// PID variable definition
float desiredSpeedL = 0;
float desiredSpeedR = 0;
float actualSpeedL = 0;
float actualSpeedR = 0;
float ErrorL = 0;
float ErrorR = 0;
float dErrorL = 0;
float dErrorR = 0;
float iErrorL = 0;
float iErrorR = 0;
float dT_sec = 0;
float lastErrorL = 0;
float lastErrorR = 0;
float P_l = 8;
float D_l = 0;
float P_r = 8;
float D_r = 0;
float I_l = 0;
float I_r = 0;
float accel[3];
float gyro[3];
float magne[3];
int dPWM_L = 0;
int dPWM_R = 0;
int PWM_L = 0;
int PWM_R = 0;
int eStopOutput;

// Encoder values
volatile int tickDataRight = 0;
volatile int tickDataLeft = 0;

// Constant Definition
const double wheelCircum = 1.092;
const double gearRatio = 32.0;
const int ticksPerRev = 48;
const double metersPerTick = wheelCircum / (ticksPerRev * gearRatio);

bool gotCommand = false;
bool nonMotorCommand = false;
int estop = 1;
char commandType;

int main() {
    wait(0.5);
    myLED1 = 1;

    // Set interrupt function
    encoderLeftPinA.rise(&tickLeft);;
    encoderRightPinA.rise(&tickRight);

    timer.reset();
    timer.start();

    wait(0.5);
    myLED1 = 0;
    // Ready to go

    while (true) {
        if (serialNUC.readable()) {
            serialNUC.scanf("%s", &buffer);
            commandType = buffer[0];

            if (commandType == '$') {
                // Give value to desiredSpeedL and desiredSpeedR
                parseCommand((char *)buffer);
                gotCommand = true;
                lastCmdTime = timer.read_ms();
                if (DEBUG) {
                    serialNUC.printf("Debug: Motor cmd Recognized\r\n");
                    serialNUC.printf("Echo Left %f, Right %f\r\n", desiredSpeedL, desiredSpeedR);
                }
            }
            else if (commandType == '#') {
                nonMotorCommand = true;
                if (DEBUG) {
                    serialNUC.printf("Debug: NonMotor cmd Recognized\r\n");
                }
            }

            if (nonMotorCommand)
            {
                switch (buffer[1])
                {
                    case 'P':
                        parseNonMotor((char *)buffer);
                        serialNUC.printf("#P%2.2f,%2.2f\r\n", P_l, P_r);
                        break;
                    case 'D':
                        parseNonMotor((char *)buffer);
                        serialNUC.printf("#D%2.2f,%2.2f\r\n", D_l, D_r);
                        break;
                    case 'I':
                        parseNonMotor((char *)buffer);
                        serialNUC.printf("#I%2.2f,%2.2f\r\n", I_l, I_r);
                        break;
                    default:
                        serialNUC.printf("#EInvalid Command\r\n");
                }
                nonMotorCommand = false;
            }
        }

        if (!TIMEOUT) {
            if (timer.read_ms() - lastCmdTime > 500) {
                serialNUC.printf("#ETIMEOUT\r\n");
                desiredSpeedL = 0;
                desiredSpeedR = 0;
                PWM_L = 0;
                PWM_R = 0;
                bothMotorStop();
            }
        }

        if (timer.read_ms() > pow(2, 20))
        {
            timer.reset();
            lastCmdTime = 0;
        }

        // Estop logic
        if (eStopStatus.read()) {
            // If get 5V, since inverted, meaning disabled on motors
            estop = 0;
            desiredSpeedL = 0;
            desiredSpeedR = 0;
            PWM_L = 0;
            PWM_R = 0;
            bothMotorStop();
            eStopLight = 1;
        }
        else {
            estop = 1;
            eStopLight = 0;
        }

        pid();
        serialNUC.printf("$%1.2f,%1.2f,%1.3f\r\n", actualSpeedL, actualSpeedR, dT_sec);
        wait_ms(13);
        serialNUC.printf("#V%2.2f,%d\r\n", battery.read() * 3.3 * 521 / 51, estop);
        wait_ms(13);

    }
}

void parseCommand(char *cmd) { 
    short index = 0;
    if (cmd[index++] != '$') {
        serialNUC.printf("#EInvalid motor format $");
        return;
    }
    desiredSpeedL = atof(&cmd[index++]);
    while (cmd[index++] != ',' && index < 30) {}

    if (index < 50) {
        desiredSpeedR = atof(&cmd[index]);
    } else {
        serialNUC.printf("#EInvalid motor format ','");
        return;
    }
}

void parseNonMotor(char *cmd) {
    short index = 1;
    char preceeding = cmd[index++];
    float val1 = atof(&cmd[2]);
    while (cmd[index++] != ',' && index < 30) {}

    float val2 = atof(&cmd[index]);

    switch (preceeding) {
    case 'P':
        P_l = val1;
        P_r = val2;
        break;
    case 'D':
        D_l = val1;
        D_r = val2;
        break;
    case 'I':
        I_l = val1;
        I_r = val2;
        break;
    default:
        serialNUC.printf("#EFormat Error from mbed Parse Command");
    }
}

void tickRight() {
    if (encoderRightPinA.read() == encoderRightPinB.read()) {
        ++tickDataRight;
    }
    else {
        --tickDataRight;
    }
}

void tickLeft() {
    if (encoderLeftPinA.read() == encoderLeftPinB.read()) {
        ++tickDataLeft;
    }
    else {
        --tickDataLeft;
    }
}

void pid() {
    dT_sec = (float)(timer.read_ms() - lastLoopTime) / 1000.0;

    if (timer.read() >= 1700) {
        timer.reset();
        lastLoopTime = 0;
    }

    lastLoopTime = timer.read_ms();
    actualSpeedL = (metersPerTick * tickDataLeft) / dT_sec;
    actualSpeedR = (metersPerTick * tickDataRight) / dT_sec;

    tickDataLeft = 0;
    tickDataRight = 0;

    ErrorL = desiredSpeedL - actualSpeedL;
    ErrorR = desiredSpeedR - actualSpeedR;

    // serialNUC.printf("ErrorL: %1.2f, ErrorR: %1.2f \r\n", ErrorL, ErrorR);

    dErrorL = ErrorL - lastErrorL;
    dErrorR = ErrorR - lastErrorR;

    iErrorL = ErrorL * dT_sec;
    iErrorR = ErrorR * dT_sec;

    dPWM_L = -(int)ceil((P_l * ErrorL + D_l * dErrorL + I_l * iErrorL));
    dPWM_R = -(int)ceil((P_r * ErrorR + D_r * dErrorR + I_r * iErrorR));

    // serialNUC.printf("dpwmL: %d, dpwmR:%d \r\n",dPWM_L, dPWM_R);

    PWM_L += dPWM_L;
    PWM_R += dPWM_R;

    PWM_L = min(255, max(-255, PWM_L));
    PWM_R = min(255, max(-255, PWM_R));

    // Deadband
    if (abs(actualSpeedL) < 0.16 && abs(desiredSpeedL) < 0.16) {
        PWM_L = 0;
    }

    if (abs(actualSpeedR) < 0.16 && abs(desiredSpeedR) < 0.16) {
        PWM_R = 0;
    }

    // PWM_L = 255;
    // PWM_R = 255;

    setLeftSpeed(PWM_L);
    setRightSpeed(PWM_R);

    // setLeftSpeed(desiredSpeedL / 2.17 * 255);
    // setRightSpeed(desiredSpeedR / 2.17 * 255);

    if (DEBUG) {
        serialNUC.printf("PWM_L: %d, PWM_R: %d\n", PWM_L, PWM_R);
    }

    /*
        Be aware that this motor board does not interface with the motor
        controller with PWM. "PWM" here are mere residue from old arduino code
        -255 to 255 values are handled in motor.cpp file, mapped to 0 to 127.
    */

    lastErrorL = ErrorL;
    lastErrorR = ErrorR;

    wait_ms(20);
}


void bothMotorStop() {
    serial.putc(0);
}

void setLeftSpeed(int c) {
    c = (c + 250) / 4 + 1;
    if (c > 127)
    {
        c = 127;
    }
    else if (c < 0)
    {
        c = 0;
    }
    c += 128;
    serial.putc(static_cast<char>(c));
}

void setRightSpeed(int c) {
    c = (c + 250) / 4 + 1;
    if (c > 127)
    {
        c = 127;
    }
    else if (c < 1)
    {
        c = 1;
    }
    serial.putc(static_cast<char>(c));
}

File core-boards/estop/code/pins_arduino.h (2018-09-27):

/*
  pins_arduino.h - Pin definition functions for Arduino
  Part of Arduino - http://www.arduino.cc/

  Copyright (c) 2007 David A. Mellis

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
  You should have received a copy of the GNU Lesser General
  Public License along with this library; if not, write to the
  Free Software Foundation, Inc., 59 Temple Place, Suite 330,
  Boston, MA  02111-1307  USA
*/

#ifndef Pins_Arduino_h
#define Pins_Arduino_h

#include <avr/pgmspace.h>

#define NUM_DIGITAL_PINS            22
#define NUM_ANALOG_INPUTS           8
#define analogInputToDigitalPin(p)  ((p < 6) ? (p) + 14 : -1)

#if defined(__AVR_ATmega8__)
#define digitalPinHasPWM(p)         ((p) == 9 || (p) == 10 || (p) == 11)
#else
#define digitalPinHasPWM(p)         ((p) == 3 || (p) == 5 || (p) == 6 || (p) == 9 || (p) == 10 || (p) == 11)
#endif

static const uint8_t SS   = 10;
static const uint8_t MOSI = 11;
static const uint8_t MISO = 12;
static const uint8_t SCK  = 13;

static const uint8_t SDA = 18;
static const uint8_t SCL = 19;
#define LED_BUILTIN 13

static const uint8_t A0 = 14;
static const uint8_t A1 = 15;
static const uint8_t A2 = 16;
static const uint8_t A3 = 17;
static const uint8_t A4 = 18;
static const uint8_t A5 = 19;
static const uint8_t A6 = 22;
static const uint8_t A7 = 23;

#define digitalPinToPCICR(p)    (((p) >= 0 && (p) <= 21) ? (&PCICR) : ((uint8_t *)0))
#define digitalPinToPCICRbit(p) (((p) <= 7) ? 2 : (((p) <= 13) ? 0 : 1))
#define digitalPinToPCMSK(p)    (((p) <= 7) ? (&PCMSK2) : (((p) <= 13) ? (&PCMSK0) : (((p) <= 21) ? (&PCMSK1) : ((uint8_t *)0))))
#define digitalPinToPCMSKbit(p) (((p) <= 7) ? (p) : (((p) <= 13) ? ((p) - 8) : ((p) - 14)))

#define digitalPinToInterrupt(p)  ((p) == 2 ? 0 : ((p) == 3 ? 1 : NOT_AN_INTERRUPT))

#ifdef ARDUINO_MAIN

// On the Arduino board, digital pins are also used
// for the analog output (software PWM).  Analog input
// pins are a separate set.

// ATMEL ATMEGA8 & 168 / ARDUINO
//
//                  +-\/-+
//            PC6  1|    |28  PC5 (AI 5)
//      (D 0) PD0  2|    |27  PC4 (AI 4)
//      (D 1) PD1  3|    |26  PC3 (AI 3)
//      (D 2) PD2  4|    |25  PC2 (AI 2)
// PWM+ (D 3) PD3  5|    |24  PC1 (AI 1)
//      (D 4) PD4  6|    |23  PC0 (AI 0)
//            VCC  7|    |22  GND
//            GND  8|    |21  AREF
//            PB6  9|    |20  AVCC
//            PB7 10|    |19  PB5 (D 13)
// PWM+ (D 5) PD5 11|    |18  PB4 (D 12)
// PWM+ (D 6) PD6 12|    |17  PB3 (D 11) PWM
//      (D 7) PD7 13|    |16  PB2 (D 10) PWM
//      (D 8) PB0 14|    |15  PB1 (D 9) PWM
//                  +----+
//
// (PWM+ indicates the additional PWM pins on the ATmega168.)

// ATMEL ATMEGA1280 / ARDUINO
//
// 0-7 PE0-PE7   works
// 8-13 PB0-PB5  works
// 14-21 PA0-PA7 works 
// 22-29 PH0-PH7 works
// 30-35 PG5-PG0 works
// 36-43 PC7-PC0 works
// 44-51 PJ7-PJ0 works
// 52-59 PL7-PL0 works
// 60-67 PD7-PD0 works
// A0-A7 PF0-PF7
// A8-A15 PK0-PK7


// these arrays map port names (e.g. port B) to the
// appropriate addresses for various functions (e.g. reading
// and writing)
const uint16_t PROGMEM port_to_mode_PGM[] = {
	NOT_A_PORT,
	NOT_A_PORT,
	(uint16_t) &DDRB,
	(uint16_t) &DDRC,
	(uint16_t) &DDRD,
};

const uint16_t PROGMEM port_to_output_PGM[] = {
	NOT_A_PORT,
	NOT_A_PORT,
	(uint16_t) &PORTB,
	(uint16_t) &PORTC,
	(uint16_t) &PORTD,
};

const uint16_t PROGMEM port_to_input_PGM[] = {
	NOT_A_PORT,
	NOT_A_PORT,
	(uint16_t) &PINB,
	(uint16_t) &PINC,
	(uint16_t) &PIND,
};

const uint8_t PROGMEM digital_pin_to_port_PGM[] = {
	PD, /* 0 */
	PD,
	PD,
	PD,
	PD,
	PD,
	PD,
	PD,
	PB, /* 8 */
	PB,
	PB,
	PB,
	PB,
	PB,
	PC, /* 14 */
	PC,
	PC,
	PC,
	PC,
	PC,
    PB,
    PB,
};

const uint8_t PROGMEM digital_pin_to_bit_mask_PGM[] = {
	_BV(0), /* 0, port D */
	_BV(1),
	_BV(2),
	_BV(3),
	_BV(4),
	_BV(5),
	_BV(6),
	_BV(7),
	_BV(0), /* 8, port B */
	_BV(1),
	_BV(2),
	_BV(3),
	_BV(4),
	_BV(5),
	_BV(0), /* 14, port C */
	_BV(1),
	_BV(2),
	_BV(3),
	_BV(4),
	_BV(5),
    _BV(6),
    _BV(7),
};

const uint8_t PROGMEM digital_pin_to_timer_PGM[] = {
	NOT_ON_TIMER, /* 0 - port D */
	NOT_ON_TIMER,
	NOT_ON_TIMER,
	// on the ATmega168, digital pin 3 has hardware pwm
#if defined(__AVR_ATmega8__)
	NOT_ON_TIMER,
#else
	TIMER2B,
#endif
	NOT_ON_TIMER,
	// on the ATmega168, digital pins 5 and 6 have hardware pwm
#if defined(__AVR_ATmega8__)
	NOT_ON_TIMER,
	NOT_ON_TIMER,
#else
	TIMER0B,
	TIMER0A,
#endif
	NOT_ON_TIMER,
	NOT_ON_TIMER, /* 8 - port B */
	TIMER1A,
	TIMER1B,
#if defined(__AVR_ATmega8__)
	TIMER2,
#else
	TIMER2A,
#endif
	NOT_ON_TIMER,
	NOT_ON_TIMER,
	NOT_ON_TIMER,
	NOT_ON_TIMER, /* 14 - port C */
	NOT_ON_TIMER,
	NOT_ON_TIMER,
	NOT_ON_TIMER,
	NOT_ON_TIMER,
};

#endif
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

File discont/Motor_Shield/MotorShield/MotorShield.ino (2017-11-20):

const int encoderRightData1 = 3;
const int encoderRightData2 = 5;
const int encoderLeftData1 = 2;
const int encoderLeftData2 = 4;
const int rightForwardSpeed = 11; //BLi
const int rightBackwardSpeed = 6; //HLi
const int rightDisable = 8;
const int leftForwardSpeed = 10;
const int leftBackwardSpeed = 9;

volatile int tickDataRight = 0;
volatile int tickDataLeft = 0;

const float ticksPerRev = 48.0;
const float gearRatio = 32.0;
const float wheelCir = 1.092; // Meters
const float metersPerTick = wheelCir / (ticksPerRev * gearRatio);
const float DEADBAND = 2;

float desiredSpeedR = 0; // m/s
float desiredSpeedL = 0; // m/s
float actualSpeedR;
float actualSpeedL;

float lastErrorL;
float lastErrorR;

float P_l = 8;
float D_l = 0;
float P_r = 8;
float D_r = 0;

int PWM_L = 0;
int PWM_R = 0;

long lastLoopTime;
float dT_sec;

double buffer_r[5] = {};
double buffer_l[5] = {};
int index = 0;
double result_r = 0;
double result_l = 0;

int powerL = 0;

// Serial comm vars
#define uchar unsigned char
uchar cmd[4] = {
  0,0,0,0};
int numBytesIn = 0;
boolean cmdHasStarted = false;
long lastCmdTime;

/* TODO
 * 1 - fix deadband (maybe bigger?)
 * 2 - push command speed
 * 3 - fix timeout
 */


void setup()
{
  Serial.begin(9600);

  pinMode(encoderRightData1, INPUT);
  pinMode(encoderRightData2, INPUT);
  pinMode(encoderLeftData1,  INPUT);
  pinMode(encoderLeftData2,  INPUT);

  digitalWrite(encoderRightData1, HIGH);
  digitalWrite(encoderRightData2, HIGH);
  digitalWrite(encoderLeftData1,  HIGH);
  digitalWrite(encoderLeftData2,  HIGH);

  pinMode(rightForwardSpeed, OUTPUT);
  pinMode(rightBackwardSpeed, OUTPUT);
  pinMode(rightDisable, OUTPUT);
  pinMode(leftForwardSpeed, OUTPUT);
  pinMode(leftBackwardSpeed, OUTPUT);
  attachInterrupt(digitalPinToInterrupt(3), tickRight, CHANGE);
  attachInterrupt(digitalPinToInterrupt(2), tickLeft, CHANGE);

  delay(1000);

  lastCmdTime = millis();
  lastLoopTime = millis();
  dT_sec = millis();

  //setPwmFrequency(6,1);
  //setPwmFrequency(9,1);

  Serial.println();
  Serial.flush();
  Serial.println("Ready");
}

boolean gotCommand = false;

void loop()
{
  gotCommand = false;
  while(Serial.available())
  {
  if(Serial.read() == '$')
  {
    desiredSpeedL = Serial.parseFloat();
    desiredSpeedR = Serial.parseFloat();
    lastCmdTime = millis();
    gotCommand = true;
  }
  }
  if(gotCommand)
  {
  Serial.print('$');
  Serial.print(actualSpeedL);
  Serial.print(',');
  Serial.print(actualSpeedR);
  Serial.print(',');
  Serial.print(dT_sec);
  Serial.print('\n');
  }
  if( millis() - lastCmdTime > 500)
  {
  Serial.println("TIMEOUT");
  desiredSpeedL = 0;
  desiredSpeedR = 0;
  PWM_L = 0;
  PWM_R = 0;
  }

  dT_sec = (float)( millis() - lastLoopTime ) / 1000.0;
  lastLoopTime = millis();
  actualSpeedL = ( metersPerTick * tickDataLeft ) / dT_sec;
  actualSpeedR = ( metersPerTick * tickDataRight ) / dT_sec;

  tickDataLeft = 0;
  tickDataRight = 0;

  delay(50);

  float ErrorL = desiredSpeedL - actualSpeedL;
  float ErrorR = desiredSpeedR - actualSpeedR;

  float dErrorL = ErrorL - lastErrorL;
  float dErrorR = ErrorR - lastErrorR;

  int dPWM_L = (int)( P_l * ErrorL + D_l * dErrorL );
  int dPWM_R = (int)( P_r * ErrorR + D_r * dErrorR );

  PWM_L += dPWM_L;
  PWM_R += dPWM_R;

  PWM_L = min(255, max(-255, PWM_L) );
  PWM_R = min(255, max(-255, PWM_R) );

  // Deadband
  if( abs(PWM_L) < 0.15 )
  PWM_L = 0;
  if( abs(PWM_R) < 0.15 )
  PWM_R = 0;

  if(PWM_L < 0) {
  analogWrite(leftForwardSpeed, 0);
  analogWrite(leftBackwardSpeed, -PWM_L);
  } else {
  analogWrite(leftForwardSpeed, PWM_L);
  analogWrite(leftBackwardSpeed, 0);
  }

  if(PWM_R < 0) {
  analogWrite(rightForwardSpeed, 0);
  analogWrite(rightBackwardSpeed, -PWM_R);
  } else {
  analogWrite(rightForwardSpeed, PWM_R);
  analogWrite(rightBackwardSpeed, 0);
  }

  lastErrorL = ErrorL;
  lastErrorR = ErrorR;
}

void tickRight()
{
  if (digitalRead(encoderRightData1) == digitalRead(encoderRightData2))
  {
  tickDataRight++;
  }
  else
  {
  tickDataRight--;
  }
}

void tickLeft()
{
  if (digitalRead(encoderLeftData1) == digitalRead(encoderLeftData2))
  {
  tickDataLeft++;
  }
  else
  {
  tickDataLeft--;
  }
}

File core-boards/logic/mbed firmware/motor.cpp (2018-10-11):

#include "motor.h"

Motor::Motor() {
    saberToothMC = new Serial(p13, NC);
    saberToothMC->baud(9600);
    stop();
}
// I will scale from -256 to 255 to 0 to 127
void Motor::setLeftSpeed(int speedL) {
    speedL = (speedL + 255) / 4 + 1;
    if (speedL > 127) {
        speedL = 127;
    } else if (speedL < 0) {
        speedL = 0;
    }
    speedL += 128;
    saberToothMC->putc(speedL);
    leftSpeed = speedL;
}

int Motor::getLeftSpeed() {
    return leftSpeed;
}
void Motor::setRightSpeed(int speedR) {
    speedR = (speedR + 255) / 4 + 1;
    if (speedR > 127) {
        speedR = 127;
    } else if (speedR < 1) {
        speedR = 1;
    }
    saberToothMC->putc(speedR);
    leftSpeed = speedR;
}

int Motor::getRightSpeed() {
    return rightSpeed;
}

void Motor::stop() {
    saberToothMC->putc(64);
    saberToothMC->putc(192);
}

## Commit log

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2014-01-23 Updates Light Shield schematic to most recent version. Renames schematic to Light_Shield.sch Adds Victor's name in the designer block.
    [Light_Shield.sch]
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2014-02-01 Chaged the Q1 and Q1 transistors, changed switch to tactile switch version
    [Light_Shield.brd, Light_Shield.sch]
2014-02-01 Redesigned configuration of board
    [Light_Shield.brd, Light_Shield.sch]
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2014-02-02 Updated version of light shield with further placement optimizations
    [Light_Shield.brd, Light_Shield.dsn, Light_Shield.sch]
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2014-02-14 Fixes layout to ensure clustered LEDs and legible labels.
    [Light_Shield.brd, Light_Shield.sch]
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2014-02-24 Moves LED labels to tNames layer so they print at OSH PArk.
    [Light_Shield.brd]
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2015-10-29 24V Rail Schematic
    Schematic for the 24V Rail
    [24V_RAIL.sch]
2015-11-05 Edited modified board design, pinout fixed
    [Motor_Shield.brd, Motor_Shield.sch]
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2017-01-03 board design v2 with complement master pin adjustments
    [MotorShieldTestbench.brd, MotorShieldTestbench.sch]
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2017-01-12 Revision Upon Review
    Label in lines applied
    Capacitors linked to 7805 Regulator value changed according to 7805
    data sheet
    General Schematics Design Cleanup
    [EncoderTBPCB.sch]
2017-01-12 Encoder Post-Review Modification
    Board Replaced upon comments given by Daniil and Ryo
    [EncoderTBPCB.brd, EncoderTBPCB.sch]
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2017-01-19 Battery and LCD Overlay
    Intended LCD position put as 22 bPlace and Potential Battery put as 21
    tPlace on the graph as Graphical reference
    [EncoderTBPCB.brd]
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2017-02-01 Serial Communication Connector Added
    Thanks @2Ryan09 for pointing that out.
    [EncoderTBPCB.brd, EncoderTBPCB.sch]
2017-02-02 Design Updated with 4 - pin Serial Connector
    [EncoderTBPCB.brd, EncoderTBPCB.sch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]
2017-02-02 Request by @ryanstrat on making it a square board
    [EncoderTBPCB.brd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]
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2017-03-12 First Version Completed
    Several Questions remain, mbed microcontroller not included, TD, RD, +-
    and D+- from ethernet Phy and main chip not connected, some pin
    connection requires verification.
    [MotorAndLightmBed.sch]
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2017-03-27 Motor and Light Initial Submit
    Primary structure completed, resistors and capacitors remained to add
    and some general arrangement issues to be resolved.
    [MotorAndLightmBed.brd, MotorAndLightmBed.sch]
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2017-04-23 Finalized
    Final Submission before design review. IMU problem remain unresolved.
    Micro-usb-b addressed.
    [MotorAndLight.sch, MotorAndLightmBed.brd, MotorAndLightmBed.sch]
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2017-04-23 fixed Power lib
    [MotorShieldTestbench.brd, MotorShieldTestbench.sch]
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2017-05-18 might need to revert upon arrival of new batteries
    [MotorShield.ino]
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2017-05-28 Pull-up network and cores. gerber file
    it’s magic
    [MotorAndLightmBed.brd, MotorAndLightmBed.sch]
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2017-06-21 Merge branch 'Motor-and-Light'
    # Conflicts:
    # Motor and Light/MotorAndLightmBed.sch
    # Testbench/Motor_Shield_Testbench/Board Design/MotorShieldTestbench.brd
    # Testbench/Motor_Shield_Testbench/Board Design/MotorShieldTestbench.sch
    [MotorAndLight.sch]
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2017-10-23 Primary Layout Complete
    Layout Complete, Sorting through Libraries
    [MotorBoardDev.brd, MotorBoardDev.sch]
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2017-10-30 Optimized and fixed formatting
    [SpeedLight.ino]
2017-10-30 Fixed indentation (again)
    Think something was wrong with my editor, had to fix indentation from Github's online editor
    [SpeedLight.ino]
2017-10-30 Fixed tabs (for the last time)
    Note to self - spaces, not tabs.
    [SpeedLight.ino]
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2017-11-02 Changes so far so Ryan3 can complete BOM
    [MotorBoardDev.brd, MotorBoardDev.sch]
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2017-11-07 Routing Finished, differential pair and silkscreen still need to be fixed.
    [MotorBoardDev.brd, MotorBoardDev.sch]
2017-11-08 Differential and Silkscreen fixed
    [MotorBoardDev.brd, MotorBoardDev.sch]
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2017-11-09 Library and Schematics cleaned, bus line rerouted, Package reworked.
    [MotorBoardDev.brd, MotorBoardDev.sch]
2017-11-10 Some more traces fixed
    [MotorBoardDev.brd, MotorBoardDev.sch]
2017-11-10 Final Fix before review
    [MotorBoardDev.brd]
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2017-11-19 Silk Screen fixed
    [MotorBoardDev.brd]
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2018-01-29 Schematics update and Control code initial commit
    Updated Motor board schematics with regard to the level shifter OE pin;
    Initial commit to the migration of arduino code for motor shield to motor board.
    [MotorBoardDev.brd, MotorBoardDev.sch]
2018-02-04 Add files via upload
    revisions from day of design review
    [RJ_IGVC_Estop.brd, RJ_IGVC_Estop.sch]
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2018-02-05 Fixed some errors, enlarged some labels, rounded edges
    [RJ_IGVC_Estop.brd, RJ_IGVC_Estop.sch]
2018-02-09 Local compilation of mbed firmware
    Currently the makefile complains a lot about the USBSerial package, will fix later
    LED blink works, will see how it handles atoi and stoi on Sunday.
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2018-02-23 Dependency Issue Fixed
    Updated dependencies, global.h, restructured main.cpp, testBench file is now working.
    [MPU9250.cpp, MPU9250.h, main.cpp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]
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2018-03-03 Temporary Update in accommodation with Raymond's parsing function
    [MotorBoardDev.brd]
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2018-03-13 Indentation Correction and Clean up#
    [main.cpp]
2018-03-29 Bug fixes and magic compilatoin
    [main.cpp, motor.cpp]
2018-04-10 PID fixed, also wrote a PID testbench
    [main.cpp, pidtestbench.cpp]
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2018-04-11 fixed motors going backwards on positive speeds
    [main.cpp]
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2018-04-15 Remove serial, fix delay in estop code
    [SPI_rf24L01_RX.ino, SPI_rf24L01_TX.ino]
2018-05-28 added timer reset for mbed timer
    [main.cpp]
2018-09-23 fix radio pins, add labels
    [RJ_IGVC_Estop.brd, RJ_IGVC_Estop.sch]
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2018-09-27 fixed +24V to safety regulator
    [logic.brd, logic.sch]
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2018-10-08 Working on the Schematic for a BareBones Arduino
    [LED.brd, LED.sch]
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2018-10-28 Added volt regulator to bring battery from 9v to 5v for board tests
    [BareBonePCB4LED.brd, BareBonePCB4LED.sch]
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2019-01-18 Fixing Board Errors
    [BareBonePCB4LED.brd, BareBonePCB4LED.sch, LED.brd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]
2019-01-21 fixing schematic
    [LED.brd, LED.sch]
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2019-01-24 Preliminary routing. Old differential pair currently bugs out, also need to fix labels
    [logic.brd, logic.sch]
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2019-01-25 fixed relay connections
    [RJ_IGVC_Estop.brd, RJ_IGVC_Estop.sch]
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2019-01-26 Fin touches, swapped 5 pin connector
    [logic.brd, logic.sch]
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2019-01-27 fixed estop board
    [RJ_IGVC_Estop.brd]
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2019-01-27 Added IGVC lbr so I have them and a fuse
    [LED.brd, LED.sch]
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2019-02-19 Revert "estop diode magic"
    This reverts commit 0d0471845709adb358787b62836d6b2af97c87b1.
    [RJ_IGVC_Estop.brd, RJ_IGVC_Estop.sch]
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2019-02-19 Logic board edit, connector spec-ed, battery voltage functionality removed and Lidar added
    [logic.brd, logic.sch]
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2019-02-23 addition of current sensor + microsd + temparature sensor
    [wireless.sch]
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2019-03-01 Switched labels to tags and finished micro sd sensor
    [wireless.sch]
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2019-03-03 Fix radio and add 3v, 5v power
    [wireless.sch]
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2019-03-03 Pin fixes
    [wireless.sch]
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2019-03-03 fixed boundaries
    [hotswap.brd]
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2019-03-03 wireless fixes
    [wireless.sch]
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2019-03-05 Fix capacitors
    [wireless.sch]
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2019-03-11 fixes from design review
    [wireless.sch]
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2019-04-07 Board functionally done, just need to make it look better
    [Diagnostic.brd, Diagnostic.sch]
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2019-04-09 +3v3 rail fix
    [RJ_IGVC_Estop.brd]
2019-04-12 Fixed Airwires
    [Diagnostic.brd]
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2019-06-08 fix silkscreen
    [hotswap.brd]
2019-08-25 Flip transistor sides so voltage does not reverse flow from V2 to V1 when V2 is higher
    [hotswap.brd, hotswap.sch]
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2019-11-03 Improve schematic layout and correct power/gnd symbols.
    [fanctrl.sch]
2019-11-03 Remove voltage regulator because 12V will come from the fan.
    [fanctrl.brd, fanctrl.sch]
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2019-11-10 Pin inversion fix
    [logic.brd, logic.sch]
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2019-11-10 Add LEDs (power, error, ready) and reset button.
    [fanctrl.brd, fanctrl.sch]
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2019-11-10 Replaced the MEGA2560 with a MEGA328p
    This is just an option; if there are reasons for using the 2560, this can certainly be reverted
    [remote-display.brd, remote-display.sch]
2019-11-10 Add CAN Controller (Module, Connector) to schematic. Label schematic sub-systems.
    [fanctrl.brd, fanctrl.sch]
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2019-11-16 fixed 5v airwire
    [estop_rx.brd]
2019-11-17 Fix CAN signal names for automatic differential routing.
    [fanctrl.brd, fanctrl.sch]
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2019-11-17 On-board temperature sensor is now sufrace mount MCP9701.
    [fanctrl.brd, fanctrl.sch]
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2019-11-17 11/17/19 I fixed the issues
    [igvc-neopixel.brd, igvc-neopixel.sch]
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2019-11-17 20191117 Reworked schematic
    [remote-display.brd, remote-display.sch]
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2019-11-23 Cleaning Up Parts Names and Part List
    Still need to decide on connectors
    [Diagnostic.brd, Diagnostic.sch, Parts List.xlsx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]
2019-11-24 Add pull-up resistor for temp probe; add schematic documentation.
    [fanctrl.brd, fanctrl.sch]
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2019-11-24 Add ISCO for programming microcontroller; improve documentation and layout of schm.
    [fanctrl.brd, fanctrl.sch]
2019-11-25 Fix merge problem.
    [fanctrl.brd, fanctrl.sch]
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2019-11-30 Revert "Final Changes"
    This reverts commit 7903053608bd51a5aa59f005e6dfdce4322bed2e.
    [Parts List.xlsx, diagnostic-main.brd, diagnostic-main.sch]
2019-11-30 Revert "Final Changes"
    This reverts commit 5b9b9e758388a5978d7fbc51625a6925a1063699.
    [Parts List.xlsx, diagnostic-main.brd, diagnostic-main.sch]
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2019-12-01 Fixing connector type
    [logic.brd, logic.sch]
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2020-01-09 Change CAN connector from 5 to 4 pin.
    [fanctrl.brd, fanctrl.sch]
2020-01-09 Finished initial board routing. Supposedly, evthg is routed, but ugly.
    [fanctrl.brd, fanctrl.sch]
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2020-01-13 1/12/2020
    Switched out 100 pin ATmega for 32 pin, put in new connectors
    [mast_panel_board.brd, mast_panel_board.sch]
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2020-01-16 Fixed routing problems. Added some docu layer.
    [fanctrl.brd, fanctrl.sch]
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2020-01-23 Redid component for LCD screen
    And broke entire board
    [remote-display.brd, remote-display.sch]
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2020-01-26 Update mast_panel_board.sch
    Replaced connectors w/LCD screens
    [mast_panel_board.sch]
2020-01-26 Revert "Update mast_panel_board.sch"
    This reverts commit efd99cb2754bcfe550521ba74416bc807029b3fb.
    [mast_panel_board.sch]
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2020-02-02 Ran ratsnest followed by ripup @; to remove airwires for design review.
    [fanctrl.brd]
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2020-02-03 Fixed a wire in the neopixel schematic
    [igvc-neopixel.sch]
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2020-02-06 Fix typo: ISCP --> ICSP.
    [fanctrl.brd, fanctrl.sch]
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2020-02-06 Fix LED Resist. values --> 470ohm
    [fanctrl.brd, fanctrl.sch]
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2020-02-06 Fix LED routing. Fix LED name (ERROR --> INVALID TEMP).
    [fanctrl.brd, fanctrl.sch]
2020-02-06 Fix decoupling CAP locations.
    [fanctrl.brd]
2020-02-06 Fix connector orientation. Change fan signal names for less confusion.
    [fanctrl.brd, fanctrl.sch]
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2020-02-06 Make RESET line routing nicer.
    [fanctrl.brd]
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2020-02-09 2/9/2020
    Cleaned up schematic, fixed pin assignments, added power plane and avr connector, changed resistor connection on CAN bus
    [mast_panel_board.brd, mast_panel_board.sch]
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2020-02-16 Fixed estop RX
    [estop_rx.brd, estop_rx.sch]
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2020-02-17 Minor fixes: LED names, Probe-PWM signal name change to PROBE-1WIRE.
    [fanctrl.brd, fanctrl.sch]
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2020-02-18 Add 60K resistor between RS pin on MCP2551 and GND. Other minor fixes.
    [fanctrl.brd, fanctrl.sch]
2020-02-19 Add crystal oscillator to ATMEGA328.
    [fanctrl.brd, fanctrl.sch]
2020-02-19 Route crystal. Misc routing improvements. Improve +5V distribution on Top layer. Add silkscreen boxes.
    [fanctrl.brd, fanctrl.sch]
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2020-02-20 Removed wrong version of BOM (correct version is on Google Drive)
    [igvc-neopixel-bom.csv]
2020-02-20 Fixed estop-tx
    [estop_rx.brd, estop_tx.brd, estop_tx.sch]
2020-02-25 2/23/19
    Changed out resistors, fixed SPI connections on board
    [mast_panel_board.brd, mast_panel_board.sch]
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2020-02-27 [v1.2] Add CAN controller chip. Increase board size. Re-route. Change oscillator footprint.
    [fanctrl.brd, fanctrl.sch]
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2020-02-27 Actually fix merge conflict.
    [fanctrl.sch]
2020-02-28 Fixes to various issues that have came up
    [Parts List.xlsx, diagnostic-main.brd, diagnostic-main.sch]
2020-02-28 final fixes before ordering
    [estop_tx.brd, estop_tx.sch]
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2020-03-03 Final Changes to Fix Glaring issues
    [diagnostic-main.brd]
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2020-03-05 reworked Resistor value for similar V1 and V2
    [hotswap.brd, hotswap.sch]
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2020-03-12 CAN Addition
    Added the new CAN Controller. Routing on the board still needs to be done.
    [mast_panel_board.brd, mast_panel_board.sch]
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2020-04-15 Revert "3/1/2020"
    This reverts commit 3611e6968998cfd50a97478803bccb5be4cedb33.
    [mast_panel_board.brd, mast_panel_board.sch]
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2020-07-17 {IC, Sensor}.lbr changes from Estop-fix
2020-08-06 fixed xml file in igvc-connector redefinition, rip my git rebase

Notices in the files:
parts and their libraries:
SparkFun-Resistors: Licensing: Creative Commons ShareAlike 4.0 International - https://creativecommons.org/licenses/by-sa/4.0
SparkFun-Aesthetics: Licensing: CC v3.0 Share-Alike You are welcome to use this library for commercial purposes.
